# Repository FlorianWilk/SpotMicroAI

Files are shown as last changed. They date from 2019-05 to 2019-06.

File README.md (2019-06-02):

# SpotMicro AI 

I started this Project because i got inspired by some very smart People/Companies and Projects out there and want to 
understand and adapt their work. It is based on existing OpenSource-Projects and uses affordable Hardware to enable other people to build their own Bots and help us to understand how to control it the way we want.

This Project is heavily work in progress and may change every day. It is NOT a working or even finished Project you might want to use. 

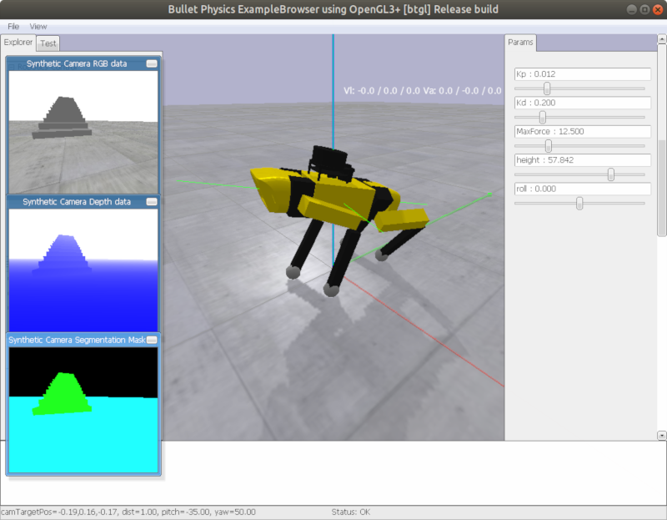
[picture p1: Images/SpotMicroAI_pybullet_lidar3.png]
PyBullet Simulation


[See the first movements of SpotMicroAI on YouTube](https://www.youtube.com/watch?v=vayiiII4xVQ)

Parts of this Project:
1. build a working physical Robot with cheap components everyone can build
2. create a simulated Environment and be able to control the Robot 
3. to do RL training to make it learn how to stand/walk/run

## 1. The physical Robot

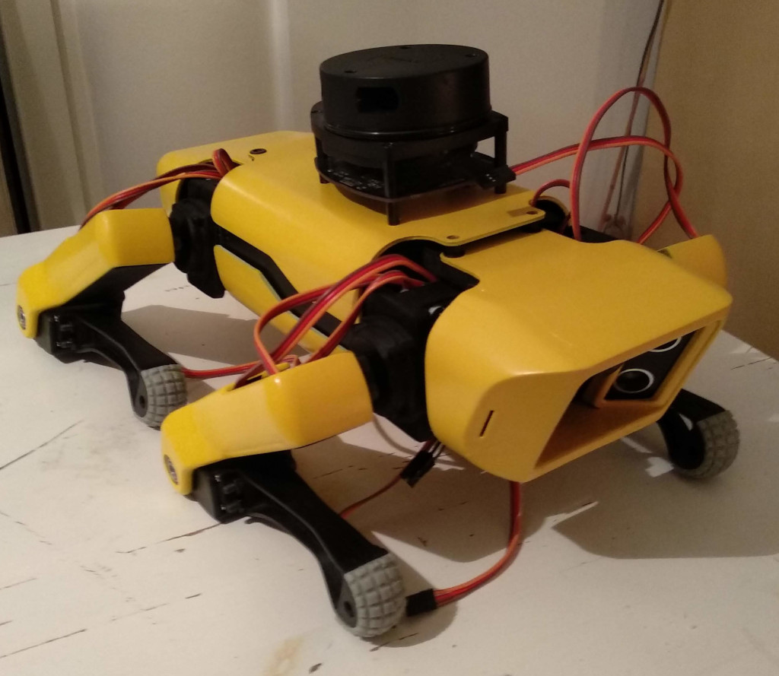
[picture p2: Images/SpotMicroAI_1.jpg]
SpotMicroAI


First of all thanks to Deok-yeon Kim aka KDY0523 who made [this incredible work on Thingiverse](https://www.thingiverse.com/thing:3445283)

This basically is the physical Robot. It will take some Days to print and assemble all the Parts, but it's worth all the effort. I also sanded, primed and painted all the Parts to give it a nicer Look.

[Here is my Thingiverse-Make](https://www.thingiverse.com/make:654812)

Since my setup required some additional Hardware, i recreated some parts using FreeCAD - see /Parts-Directory.

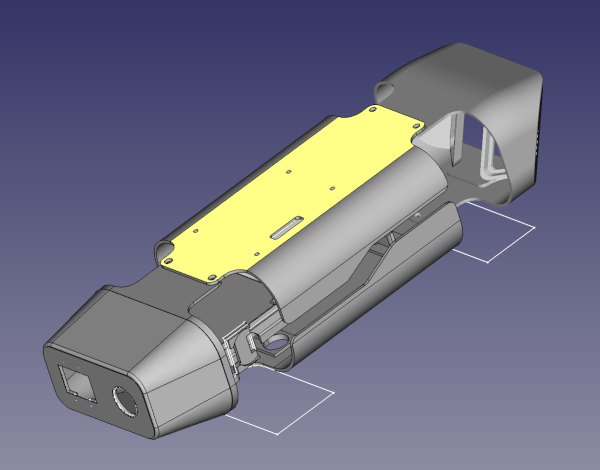
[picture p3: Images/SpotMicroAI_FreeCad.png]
Parts


### NVIDIA Jetson Nano

To have some Protection for the NVIDIA Jetson Nano i printed [this Case from Thingiverse](https://www.thingiverse.com/thing:3603594).

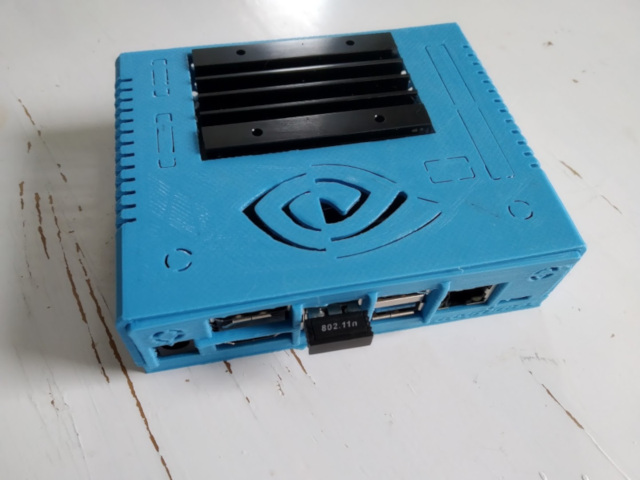
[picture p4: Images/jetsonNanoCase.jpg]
JetsonNano-Case


The Jetson Nano is connected to a 16 Channel PCA9685 I2C-Servo Driver which controls all the Servos. 
I will also try to connect the I2C OLED Display and the LED-Circle to it.

[Here you can find the all the Code for the Jetson Nano](/JetsonNano)

### Sensors

Since i am not a robotics company, i can't easily invest some hundreds of Euros/Dollars. So i will use Sonar Sensors instead of visual sensors like RGB or RGBD-Cams. Maybe i will try with ESPEyes or something in the near future.

Sensors used:
- 4 x HC-SR04-Sensors. 2x as in the original model in the front looking forward/down. 2x at the bottom (front/back) looking down to measure the ground-distance. 
- An IMU MPU-6050 is used to measure pitch,roll and velocities. Yaw will be ignored since it drifts quickly. 

Also i have a SSD1306 OLED-Display and a NeoMatrix LED-Circle i want to include for the Style.
In a first version i used an Arduino Mega as kind of Servo/Sensor-Controller and a Raspberry PI as Locomotion-Controller (communication via UART). But it showed up that the Arduino is too slow to handle Sensor-Signals and Servo-PWM properly at the same time. 

I am not sure if the Hardware i use now will be enough to finally have a very smooth walking Robot like for Example the real SpotMini. See this more as a Research-Project where I try to use cheap Hardware and other People's Work to learn more about how this all works. 

## 2. Simulation

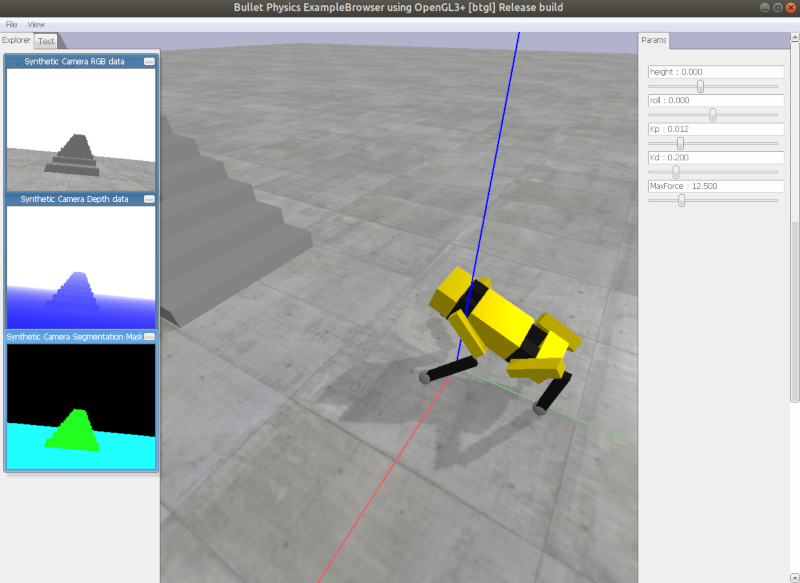
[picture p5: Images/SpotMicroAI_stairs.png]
PyBullet


I try to implement the Ideas of [this Paper](https://arxiv.org/pdf/1804.10332.pdf) by
Jie Tan, Tingnan Zhang, Erwin Coumans, Atil Iscen, Yunfei Bai, Danijar Hafner, Steven Bohez, and Vincent Vanhoucke
Google Brain,Google DeepMind

Here you can see the first version of the URDF-Model.

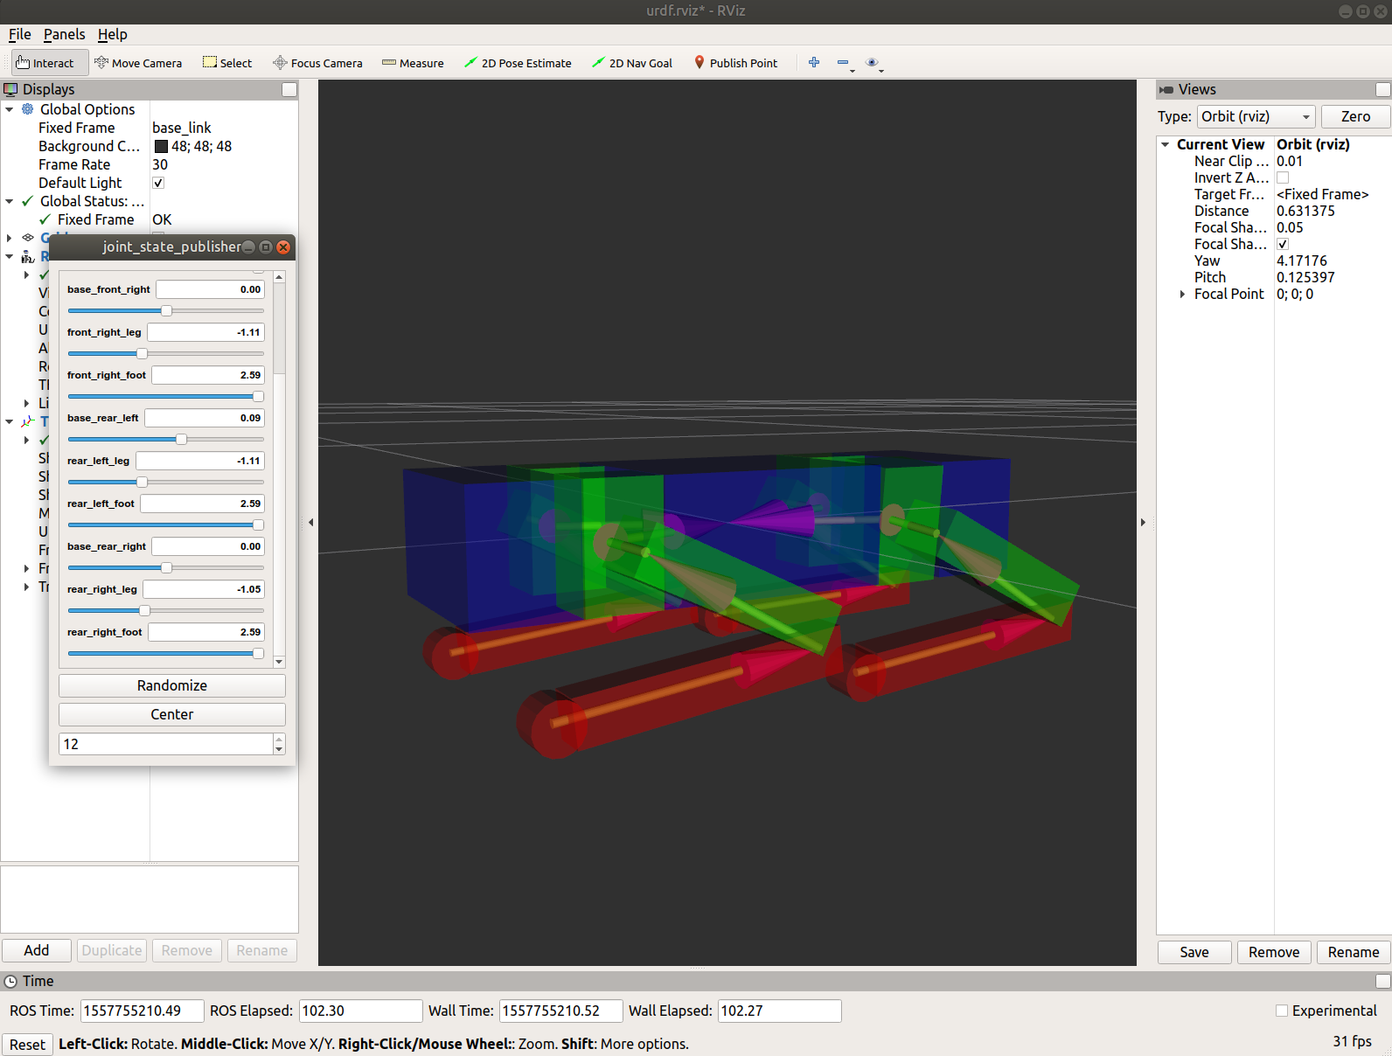
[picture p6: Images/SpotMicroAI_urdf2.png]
urdf


And here the Model with working Kinematics in a PyBullet-Simulation.

The URDF Model is very basic and work in progress. Masses and Inertias are guesses and not correct. I will have to disassemble the Robot to have correct weights. 

### Quickstart

This example can be found in the Repository. You need a GamePad for this to work:
```
pip3 install numpy
pip3 install pybullet
pip3 install inputs

cd Core/
python3 example_leg_motion.py
```

### Kinematics

In order to be able to move the Robot or event make it walk, we need something which tells us what servo-angles
will be needed for a Leg to reach position XYZ.
This is what InverseKinematics does. We know all the constraints, the length of the legs, how the joints rotate and where they are positioned. 

You can find [some a first draft of the calculations here](https://github.com/FlorianWilk/SpotMicroAI/tree/master/Kinematics). There is also a [Jupyter Notebook explaining the Kinematics](https://github.com/FlorianWilk/SpotMicroAI/tree/master/Kinematics/Kinematic.ipynb) and a [YouTube-Video](https://www.youtube.com/watch?v=VSkqhFok17Q).

## 3. Training

There is no real Training-Code yet.

## Credits and thanks

- Deok-yeon Kim creator of SpotMicro
- Boston Dynamics who built this incredible SpotMini,
- Ivan Krasin - https://ivankrasin.com/about/ - thanks for inspiration and chatting
- Jie Tan, Tingnan Zhang, Erwin Coumans, Atil Iscen, Yunfei Bai, Danijar Hafner, Steven Bohez, and Vincent Vanhoucke
Google Brain,Google DeepMind

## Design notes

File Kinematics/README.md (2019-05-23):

# How to solve Kinematics of a four-legged Robot

What is Kinematics / IK? 
A RobotLeg consists of 3 Servos rotating things from angle amin to angle amax.
When we know all three angles, we can determine the TargetPoint of the Leg.

This is what is called "Forward Kinematics". Inverse Kinematics is, you can imagine, the inverse. 
So, we have a Point and want to know the angles of our Servos. This can become pretty challenging when having more than 3-DOF (Degrees of Freedom).

See [this Page](https://www.ijstr.org/final-print/sep2017/Inverse-Kinematic-Analysis-Of-A-Quadruped-Robot.pdf) for more Information about Inverse Kinematics for quadruped Robots.
We will have to do our own calculations, since SpotMicro has some specialities which are not included a those formulas.

When you take a look at Fig. 2 you will notice, that the Leg used here is quite similar to 
SpotMicros Leg, but not really the same:

- the "Leg"-Motor/Rotation is on the same axis (z3) as the Shoulder-Motor/Rotation-Axis.
  SpotMicros Leg-Rotation is about 1cm lower, so we need an additional "L1b" which goes down (same direction as L2),
  but does not rotate with the Leg (L2,L3). Since we are completely recreating the calculations, i decided to go with
  L1-L4 instead of L1,L1b,L2,L3. 
- the "Foot"-joint is shifted by ~1cm to "the front" (pictures will follow). 

## Leg IK

So let's take a look at SpotMicro's Legs:

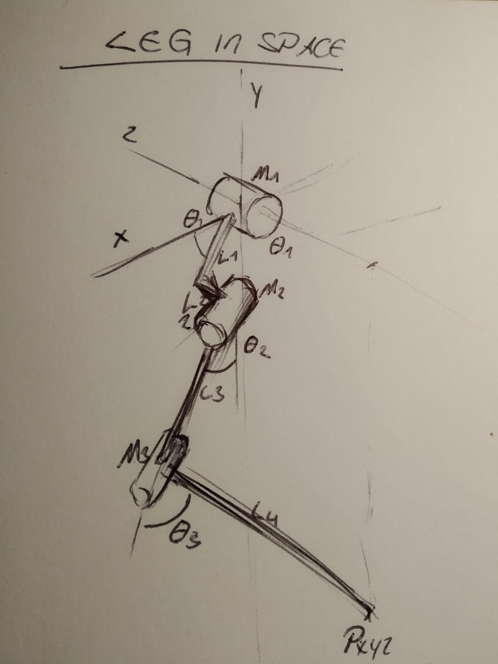
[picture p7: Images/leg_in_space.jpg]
Leg in Space


First of all lets focus on the shoulder-angle - theta1.
The Paper uses

Original

theta2

theta3

D

Let's discover that.
We need some kind of toolbelt for this mission.

### Tool 1: Pythagoras

Calculate the missing edge-length of a triangle with a 90° angle. 

Pythagoras

Pythagoras

Pythagoras

and so 

Pythagoras

Pythagoras

Pythagoras

### Tool 2: atan2(y,x) - get the angle of Point(x,y) from Origin (square-angle needed)

Please see [Wikipedia](https://en.wikipedia.org/wiki/Atan2). They did a great job in explaining it. 

### Tool 2b: get alpha angle of triangle when all sides are known

google

and yes, knowing that:

atan2

it looks very similar to:

D

theta3

### solving theta1 

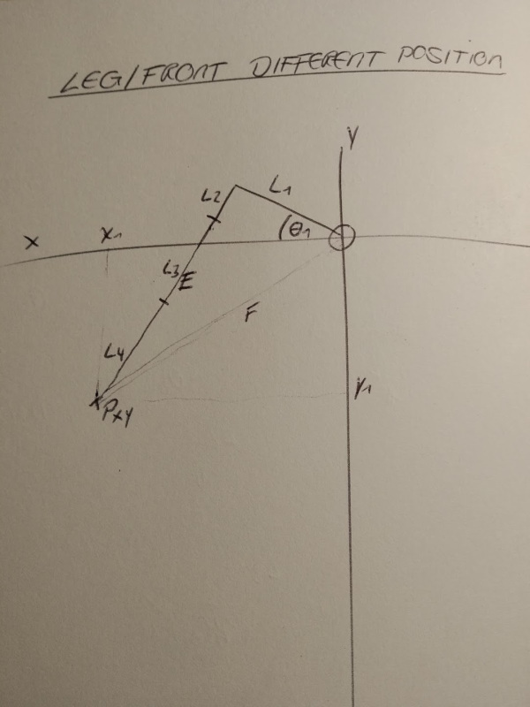
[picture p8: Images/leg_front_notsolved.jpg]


If we could solve E and F, we could calculate the angles and we have theta1!

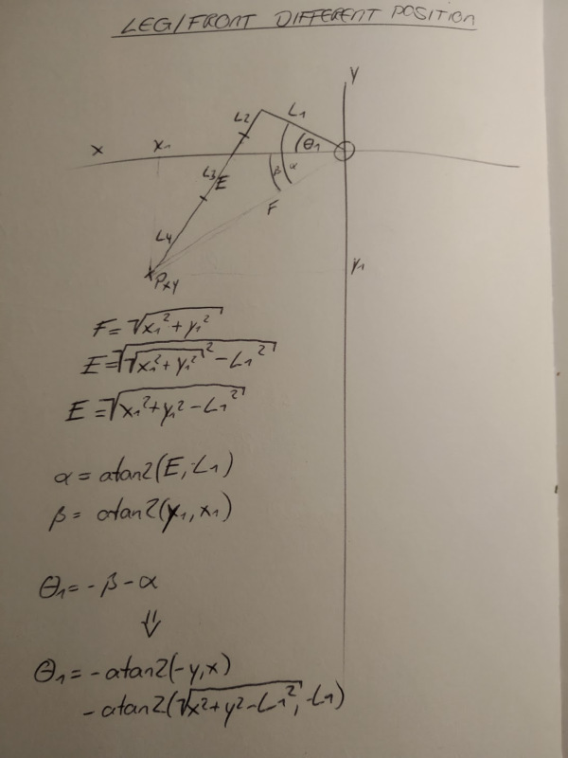
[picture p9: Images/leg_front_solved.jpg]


F is quite easy, as Pythagoras told us. And then E is quite easy too. Pythagoras again. 
Now we have a Triangle with L1,E and F, and it has a square-angle. Perfect for atan2!
So we calculate the whole angle alpha of the triangle and then substract the angle 
of the lower part by using atan2 again with -y and x. Great!

And now we have E. And E-L2 is "how long must the two joints leg and foot be (on X/Y only) to reach point Pxy".
We call it G.

g

So now we can say H is the "needed length of our joints in X,Y,Z". Thank you Pythagoras, again.

h

### solving theta3

We know what length we need to reach with the leg and foot-joint. It's a simple triangle.
All sides are known. L3,L4 and H.

D

theta3

### solving theta2

The last one, theta2. This one is quite easy:

Formula will follow

## Body Forward Kinematics

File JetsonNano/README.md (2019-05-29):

## SpotMicroAI for JetsonNano

The Nano will use a 16 Channel PCA9685 I2C-Servo Driver to drive the 12 Servos for the Legs.
First of all all prepare your Jetson Nano as you see in the NVIDIA Documentation.

Then connect to it via SSH and:

```
git clone https://github.com/FlorianWilk/SpotMicroAI.git
cd SpotMiroAI/JetsonNano
sudo apt-get install python3 python3-pip
pip3 install -U -r requirements.txt 
python3 start_robot.py
```

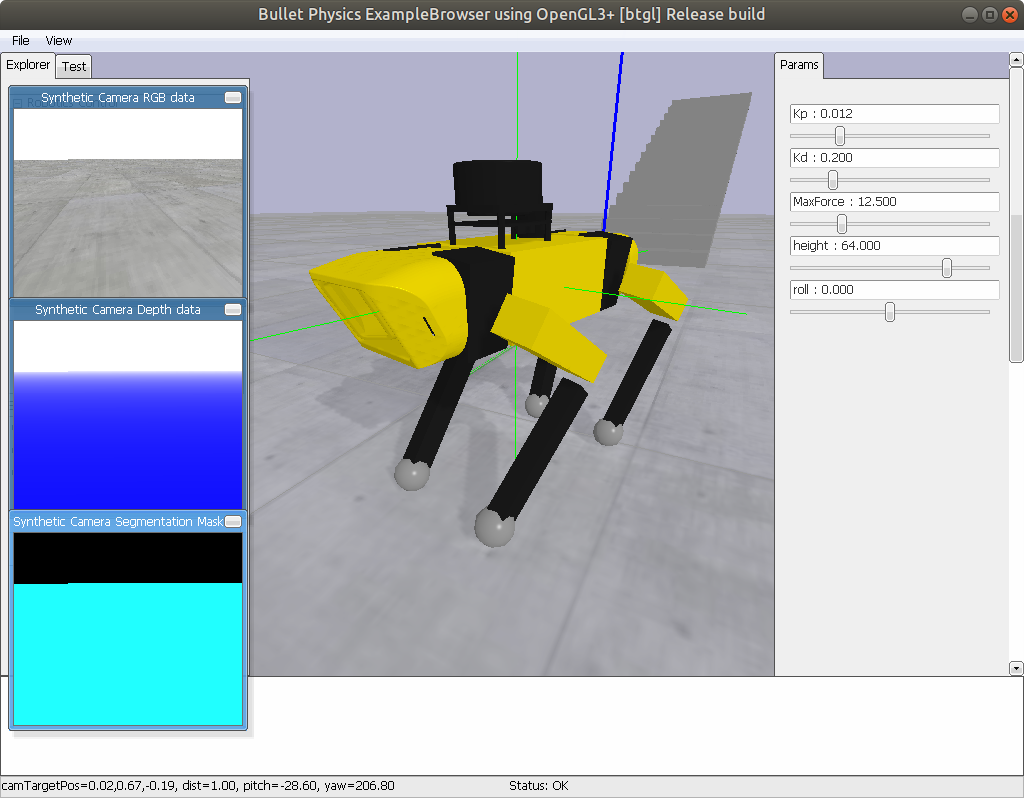
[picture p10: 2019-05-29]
Images/SpotMicroAI_pybullet_lidar.png

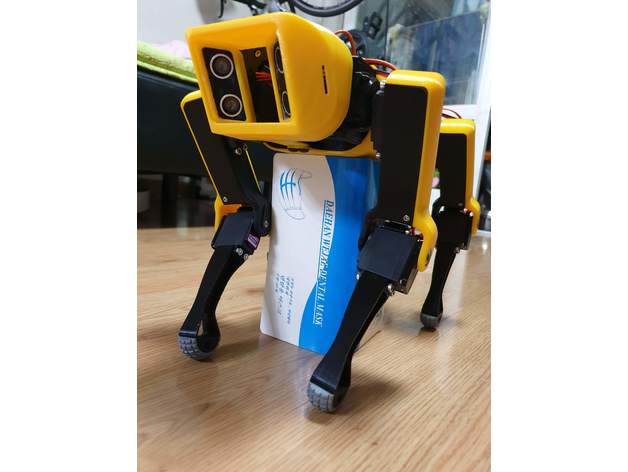
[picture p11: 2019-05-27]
STL/images/fc06bc6fa5a64951cc53c8cbf75a2861_preview_featured.jpg

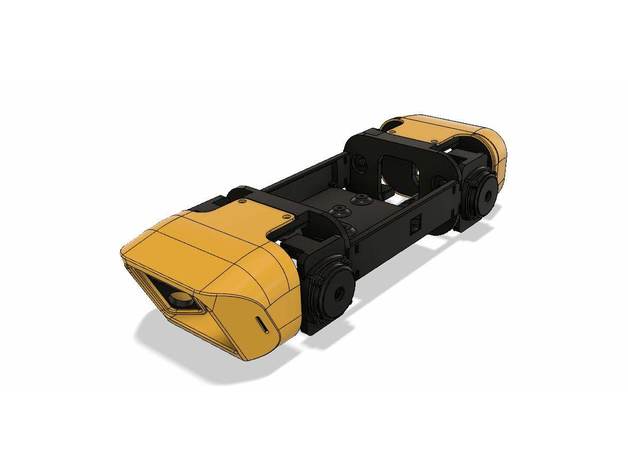
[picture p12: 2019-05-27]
STL/images/3bb4c0507fb43316081c01f398e9859c_preview_featured.jpg

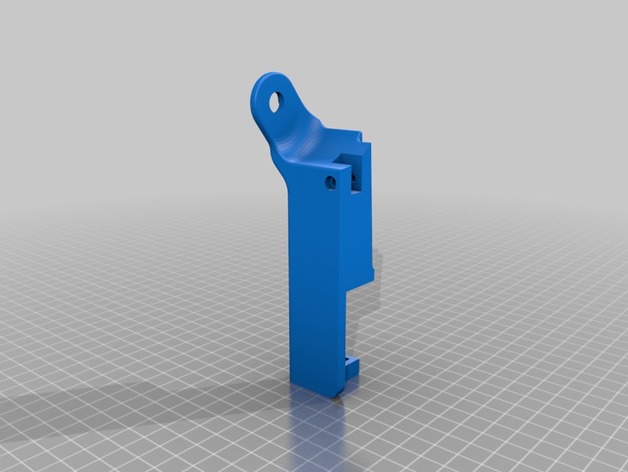
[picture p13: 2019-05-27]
STL/images/73ad5de99660dfc74a26c2a1477aee45_preview_featured.jpg

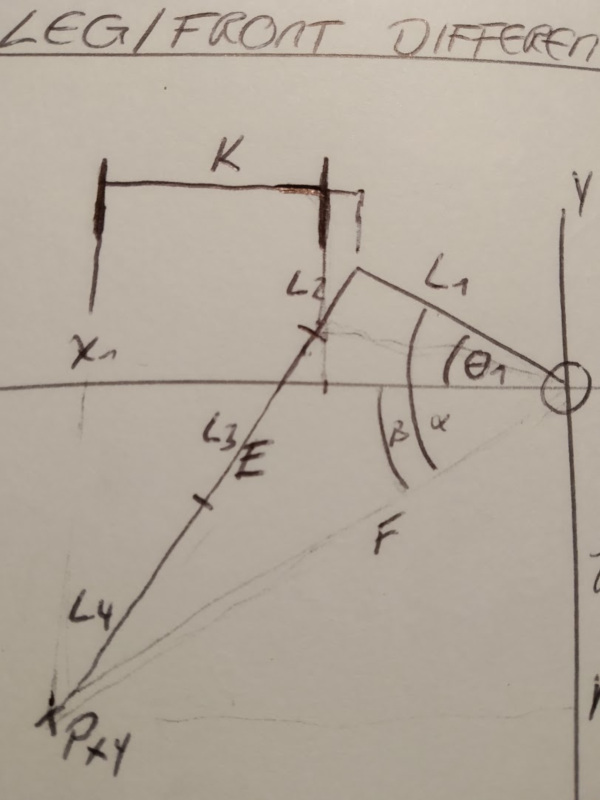
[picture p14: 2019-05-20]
Images/leg_front_k.jpg

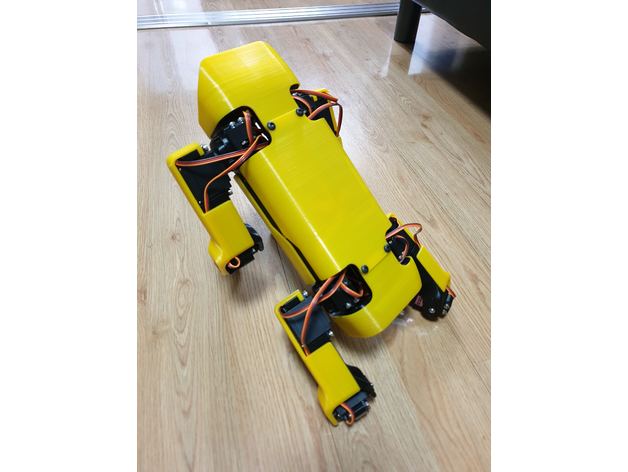
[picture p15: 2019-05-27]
STL/images/ada5e9392d64d278e71dfaec82ce3266_preview_featured.jpg

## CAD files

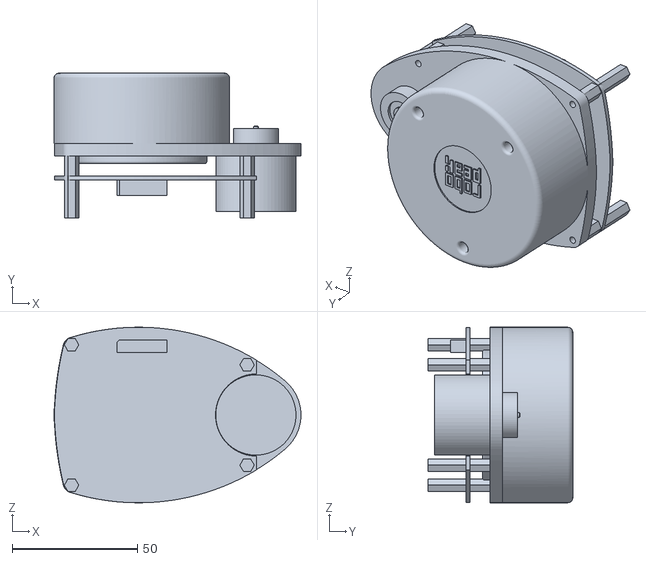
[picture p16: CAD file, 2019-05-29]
STL/lidar/rplidar_main.STL
98.5 x 57.7 x 70.0

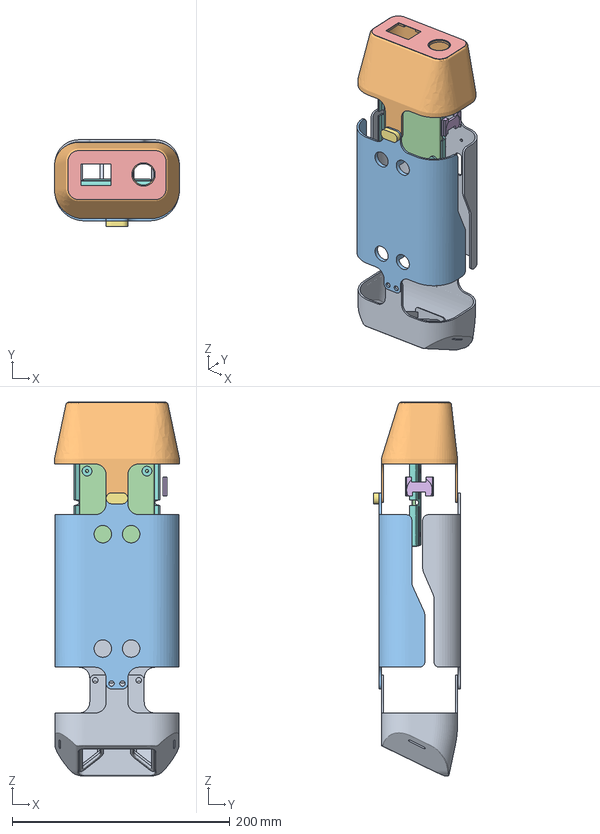
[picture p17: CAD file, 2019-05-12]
Parts/SpotMicroAI_AdditionalParts.FCStd
114.8 x 79.5 x 343.2 mm
Top
Rear
Bottom
BatteryHolderHolder
rearlabel
LEDMount
ScrewGuard
F_cover

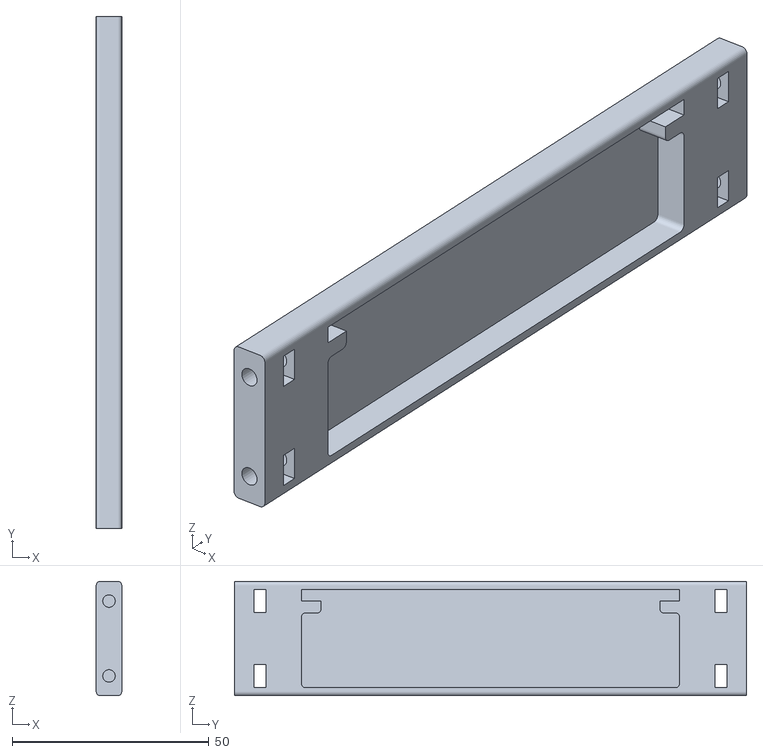
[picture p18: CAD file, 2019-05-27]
STL/files/R_side_plate.stl
6.50 x 130.0 x 29.0

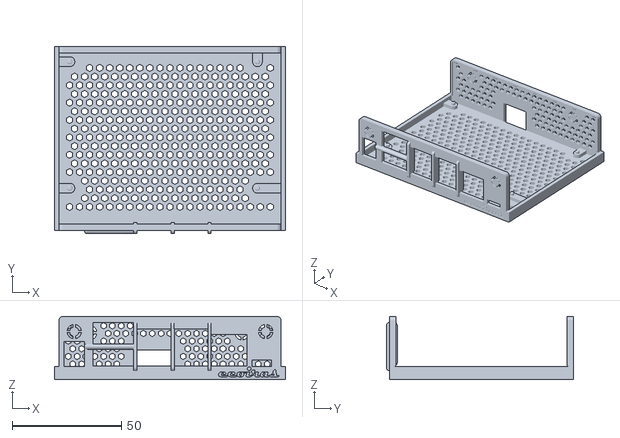
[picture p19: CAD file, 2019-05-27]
STL/jetsonnano/files/NanoBoxConnect_v11_Bottom.stl
105.9 x 85.8 x 29.0

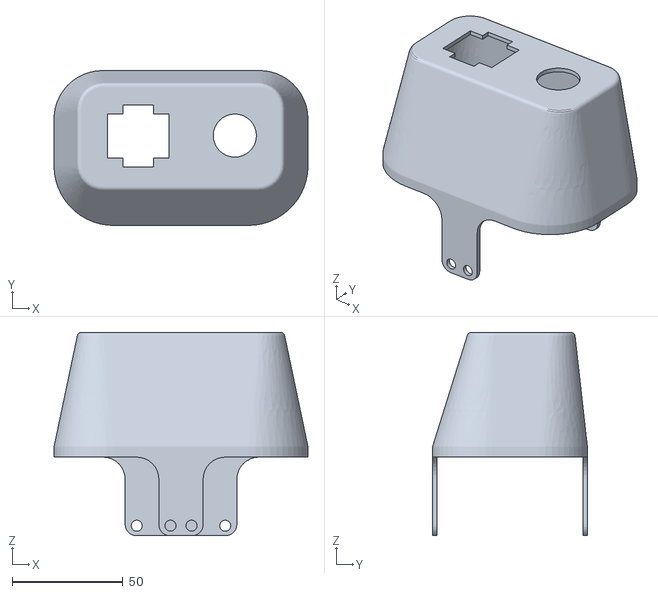
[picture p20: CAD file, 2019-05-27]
STL/rear2.stl
114.8 x 70.0 x 91.9

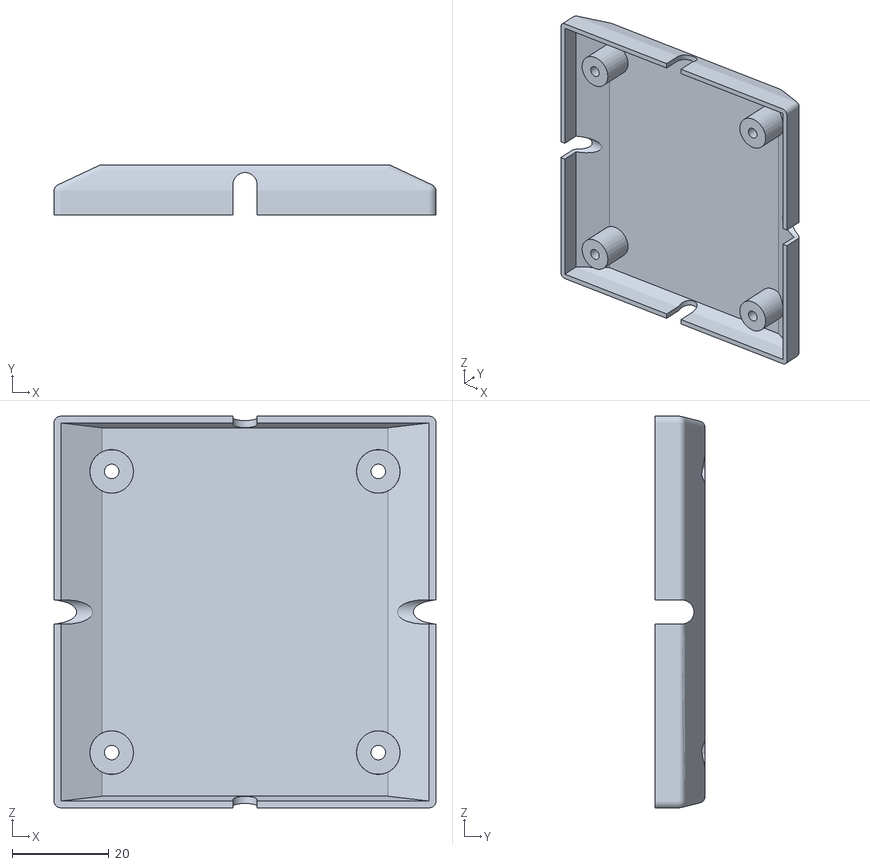
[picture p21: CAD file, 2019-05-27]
STL/batteryholder2.stl
78.8 x 10.4 x 80.8

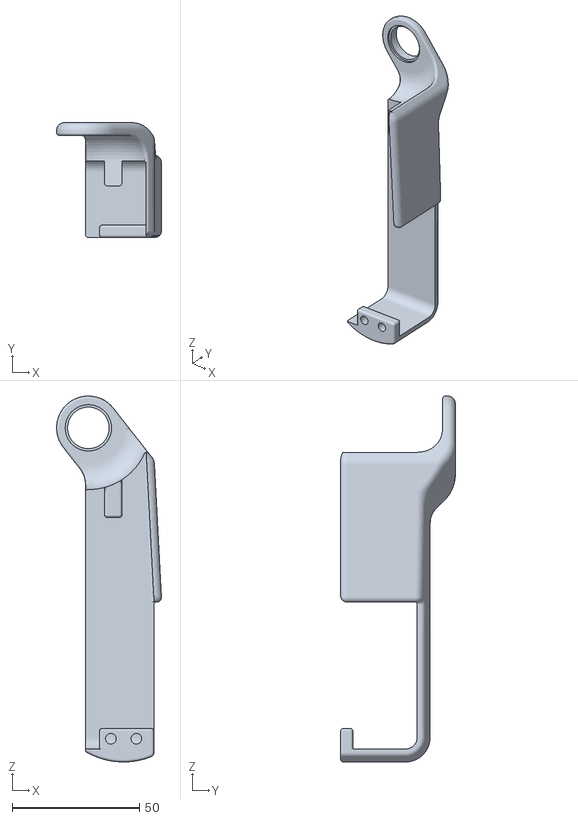
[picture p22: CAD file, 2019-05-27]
STL/files/L_arm_cover.stl
41.2 x 45.0 x 143.5

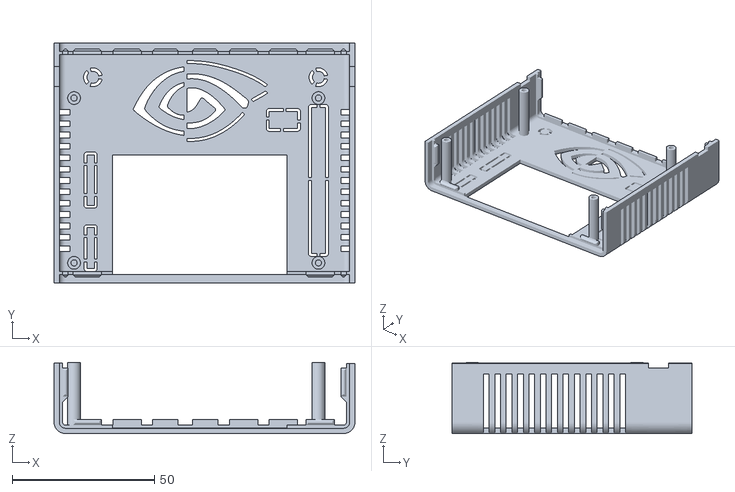
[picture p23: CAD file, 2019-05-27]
STL/jetsonnano/files/NanoBoxConnect_v11_Top.stl
105.9 x 84.3 x 25.0

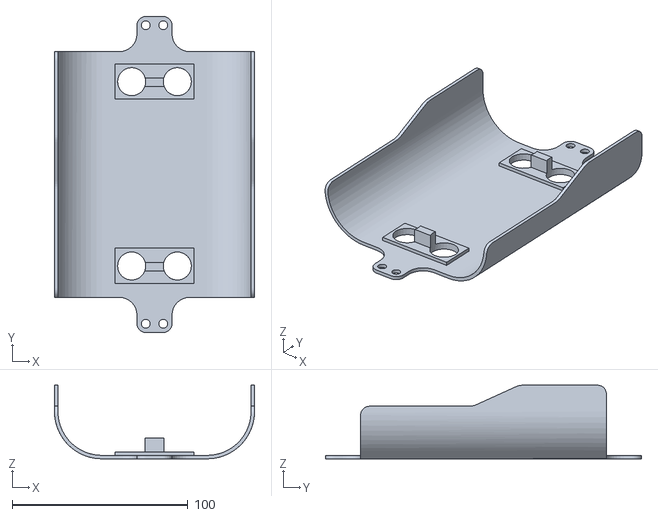
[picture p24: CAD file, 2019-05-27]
STL/bottom.stl
114.0 x 180.0 x 42.0

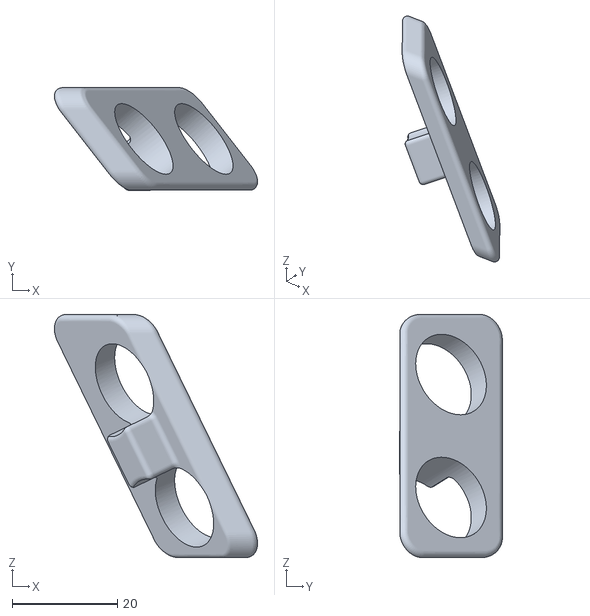
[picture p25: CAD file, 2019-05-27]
STL/files/L_ultra_sonic.stl
38.6 x 19.5 x 46.2

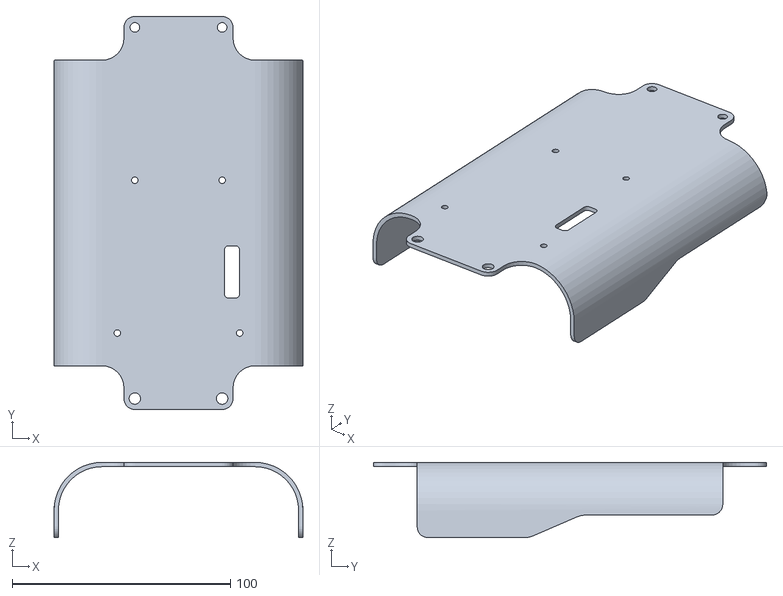
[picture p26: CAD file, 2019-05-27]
STL/top.stl
114.0 x 180.0 x 34.5

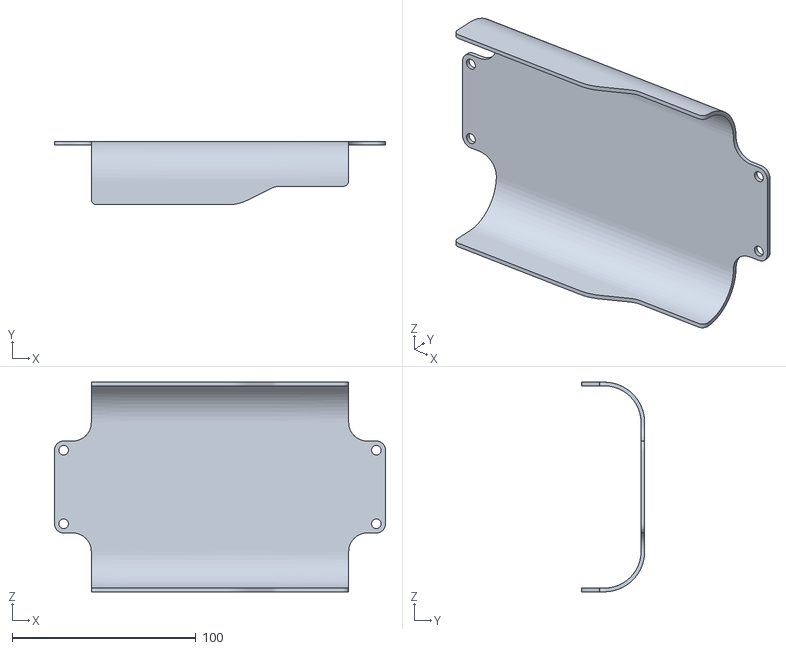
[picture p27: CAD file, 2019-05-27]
STL/files/non-mega_T_cover.stl
180.0 x 34.5 x 114.0

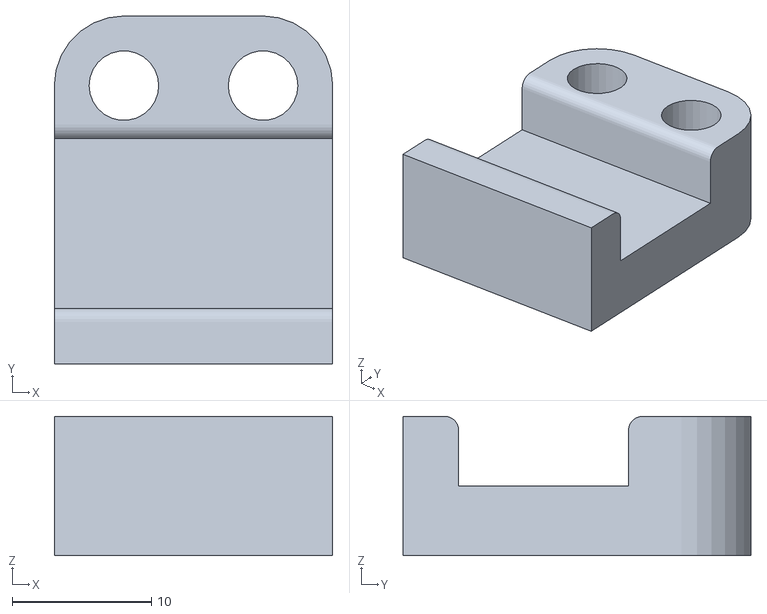
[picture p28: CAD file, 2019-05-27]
STL/testmount.stl
20.0 x 25.0 x 10.0

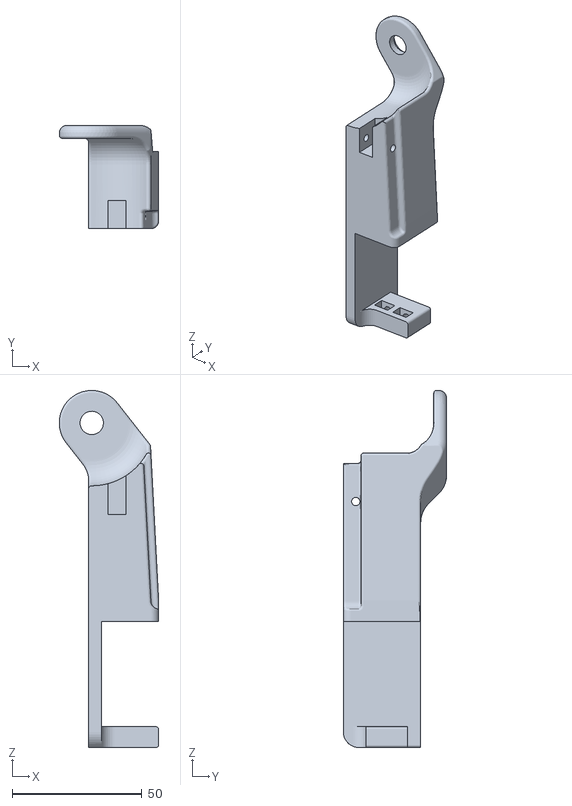
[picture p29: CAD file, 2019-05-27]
STL/files/R_arm.stl
38.2 x 39.8 x 137.4

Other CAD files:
STL/files/non-mega_L_side_plate.stl
STL/ledholder.stl
STL/files/R_arm_joint.stl
STL/batteryholder.stl
STL/files/B_cover.stl
STL/files/F_cover.stl
STL/files/F_cover_orig.stl
STL/files/F_shoulder.stl
STL/files/L_arm.stl
STL/files/L_arm_joint.stl
STL/files/L_side_plate.stl
STL/files/L_wrist.stl
STL/files/R_arm_cover.stl
STL/files/R_cover.stl
STL/files/R_shoulder.stl
STL/files/R_ultra_sonic.stl
STL/files/R_wrist.stl
STL/files/T_cover.stl
STL/files/foot.stl
STL/files/non-mega_B_cover.stl
STL/files/plate.stl
STL/label.stl
STL/rear.stl
STL/screwguard.stl

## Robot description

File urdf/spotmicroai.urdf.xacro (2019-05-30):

<?xml version="1.0"?>
<robot xmlns:xacro="http://www.ros.org/wiki/xacro" name="SpotMicroAI">

  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

  <xacro:property name="body_length" value="0.140" />
  <xacro:property name="body_width" value="0.110" />
  <xacro:property name="body_height" value="0.070" />

  <xacro:property name="lidar_length" value="0.0985" />
  <xacro:property name="lidar_width" value="0.0577" />
  <xacro:property name="lidar_height" value="0.070" />


  <xacro:property name="front_length" value="0.058" />
  <xacro:property name="rear_length" value="0.040" />

  <xacro:property name="shoulder_length" value="0.044" />
  <xacro:property name="shoulder_width" value="0.038" />

  <xacro:property name="leg_length" value="0.120" />
  <xacro:property name="foot_length" value="0.155" />

  <xacro:property name="toe_radius" value="0.020" />
  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
  <xacro:property name="toe_width" value="0.020" />
  <xacro:property name="shift" value="0.052" />
  <xacro:property name="shiftx" value="0.093" />
  <xacro:property name="shifty" value="0.036" />

  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

  <xacro:macro name="gen_shoulder" params="name left">
    <link name="${name}">
      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
      <inertial>
        <mass value="0.10"/>
        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
      </inertial>
    </link>
  </xacro:macro>

  <xacro:macro name="gen_shoulder_joint" params="pos shiftx shifty">
    <joint name="${pos}_shoulder" type="revolute">
      <parent link="base_link"/>
      <child link="${pos}_shoulder_link"/>
      <axis xyz="1 0 0"/>
      <origin rpy="0 0 0" xyz="${shiftx} ${shifty} 0"/>
      <limit effort="1000.0" lower="-0.548" upper="0.548" velocity="0.7"/>
      <dynamics damping="0.0" friction="0.5"/>
    </joint>
  </xacro:macro>

  <xacro:macro name="gen_leg" params="name">
    <link name="${name}">
      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
      <inertial>
        <mass value="0.15"/>
        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
      </inertial>
    </link>
  </xacro:macro>

  <xacro:macro name="gen_leg_joint" params="pos shift">
    <joint name="${pos}_leg" type="revolute">
      <parent link="${pos}_shoulder_link"/>
      <child link="${pos}_leg_link"/>
      <axis xyz="0 1 0"/>
      <origin rpy="0 0 0" xyz="0 ${shift} 0"/>
      <limit effort="1000.0" lower="-2.666" upper="1.548" velocity="0.5"/>
      <dynamics damping="0.0" friction="0.0"/>
    </joint>
  </xacro:macro>

  <xacro:macro name="gen_foot" params="name">
    <link name="${name}">
      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
      <inertial>
        <mass value="0.1"/>
        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
      </inertial>
    </link>
  </xacro:macro>

  <xacro:macro name="gen_foot_joint" params="pos">
    <joint name="${pos}_foot" type="revolute">
      <parent link="${pos}_leg_link"/>
      <child link="${pos}_foot_link"/>
      <axis xyz="0 1 0"/>
      <origin rpy="0 0 0" xyz="-0.01 0 -${leg_length}"/>
      <limit effort="1000.0" lower="-0.1" upper="2.59" velocity="0.5"/>
      <dynamics damping="0.0" friction="0.5"/>
    </joint>
  </xacro:macro>

  <xacro:macro name="gen_toe" params="name">
    <link name="${name}">
      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
      <inertial>
        <mass value="0.05"/>
        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
      </inertial>
    </link>
  </xacro:macro>

 <xacro:macro name="gen_toe_joint" params="pos">
    <joint name="${pos}_toe" type="fixed">
      <parent link="${pos}_foot_link"/>
      <child link="${pos}_toe_link"/>
      <origin xyz="0 0 -${foot_length+0.01}"/>
    </joint>
  </xacro:macro>

  <xacro:macro name="gen_full_leg_joint" params="pos shiftx shifty shift left">
    <xacro:gen_shoulder name="${pos}_shoulder_link" left="${left}"/>
    <xacro:gen_leg name="${pos}_leg_link"/>
    <xacro:gen_foot name="${pos}_foot_link"/>
    <xacro:gen_toe name="${pos}_toe_link"/>

    <xacro:gen_shoulder_joint pos="${pos}" shiftx="${shiftx}" shifty="${shifty}"/>
    <xacro:gen_leg_joint pos="${pos}" shift="${shift}"/>
    <xacro:gen_foot_joint pos="${pos}"/>
    <xacro:gen_toe_joint pos="${pos}"/>
  </xacro:macro>

  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

  <link name="base_link">
    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
    <inertial>
      <mass value="0.80"/>
      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
    </inertial>
  </link>

  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

   <link name="lidar_link">
    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
    <inertial>
      <mass value="0.50"/>
      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
    </inertial>
  </link>
  <joint name="base_lidar" type="fixed">
    <parent link="base_link"/>
    <child link="lidar_link"/>
        <origin xyz="0 0 ${body_height/2}"/>
  </joint>  

  <link name="rear_link">
    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
    <inertial>
      <mass value="0.20"/>
      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
    </inertial>
  </link>
  <joint name="base_rear" type="fixed">
    <parent link="base_link"/>
    <child link="rear_link"/>
  </joint>

  <link name="front_link">
    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
    <inertial>
      <mass value="0.20"/>
      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
    </inertial>

  </link>
  <joint name="base_front" type="fixed">
    <parent link="base_link"/>
    <child link="front_link"/>
  </joint>

  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

  <xacro:gen_full_leg_joint pos="front_left" shiftx="-${shiftx}" shifty="-${shifty}" shift="-${shift}" left="true"/>
  <xacro:gen_full_leg_joint pos="front_right" shiftx="-${shiftx}" shifty="${shifty}" shift="${shift}" left="false"/>
  <xacro:gen_full_leg_joint pos="rear_left" shiftx="${shiftx}" shifty="-${shifty}" shift="-${shift}" left="true"/>
  <xacro:gen_full_leg_joint pos="rear_right" shiftx="${shiftx}" shifty="${shifty}" shift="${shift}" left="false"/>

</robot>

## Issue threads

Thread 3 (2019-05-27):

Python 2.7 compatibility

FlorianWilk, 2019-05-27:
Interesting... when running
python3 gamepad.py
everything works. The Bot falls to the ground and keeps standing.
When i use python 2.7:
python gamepad.py
The Bot falls down. The left and right legs have different positions. Why is that?!

littleggghost, 2019-05-27:
I use python2.7 now, here is the initial pose:
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

FlorianWilk, 2019-05-27:
Yes, same here. I will keep on using Python3 to have some progress on the
Kinematics.
Maybe you want to investigate this bug? I have no clue why Python2.7 should
do different calculations than Python3 does.

On Mon, May 27, 2019 at 1:50 PM littleggghost <notifications@github.com>
wrote:

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

littleggghost, 2019-05-27:
Maybe the initial command caused this.
You can try this initial pose in gamepad.py:
`line224    angles = kin.calcIK(Lp, (math.pi/180*roll, 0, 0), (100/256*-joy_rz-20+100, 40+height, joy_x))`

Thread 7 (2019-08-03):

Where can I find the STL file for a plate to mount an Nvidia Jetson Nano?

ashishk88, 2019-08-03:
Great work on the Spot Micro and thanks for open sourcing your work! I will really appreciate if you could point me to the location of a plate to mount an Nvidia Jetson Nano.

ashishk88, 2019-08-03:
It will be great if you could also upload the STL for the top cover with holes for LiDAR mounting.

jdmueller, 2019-08-03:
https://github.com/FlorianWilk/SpotMicroAI/blob/master/STL/top.stl

jdmueller, 2019-08-03:
https://github.com/FlorianWilk/SpotMicroAI/blob/master/urdf/stl/jetsonPlate.stl

ashishk88, 2019-08-03:
Thanks a lot!

Closed 2019-08-03.

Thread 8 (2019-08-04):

Electrical Wiring Diagram

mschwab87, 2019-08-04:
Could you possibly provide a wiring diagram?

jimprince, 2019-08-16:
what hardware are you looking for a wiring diagram for? For the PCA 9685 to the Jetson Nano or for the servos to the PCA9685? Or something else?

mschwab87, 2019-08-16:
Hey Brad,

We were able to figure it out. When we started the project we were just
wondering if there was a wiring diagram for the the whole system servos to
pca, pca to jetson etc. Thanks for getting back to me.

Regards,

Matt

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

jimprince, 2019-08-16:
No worries. Let me know if you have any other questions.

Closed 2019-08-17.

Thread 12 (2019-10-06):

Problems with running the examples - stl files

Brudasoe, 2019-10-06:
Hey, so I had some problems with running the bullet python examples, the source of those problems is that thought the stl files have beenample moved, urdf files haven't really been updated (rplidar_main.stl is missing and some tags point to foot.stl in STL folder (which has been removed). I can make a PR to fix this issues if you want :slightly_smiling_face:

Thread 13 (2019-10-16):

kinematic.py file is lost

mushroom-x, 2019-10-16:
after excute  the first cell of script   `Kinematic/KinematicMovements.ipynb , `
error message as bellow:
```
---------------------------------------------------------------------------
ModuleNotFoundError                       Traceback (most recent call last)
<ipython-input-2-905fcd046da8> in <module>
      6 import pybullet as p
      7 import pybullet_data
----> 8 from kinematics import Kinematic
      9
     10 p.connect(p.DIRECT)

ModuleNotFoundError: No module named 'kinematics'

```

Brudasoe, 2019-10-21:
Parts of code have been moved, but I guess not all parts have been updated ( I had an issue with stl files),  seems like you need to modify the code to point to Core/kinematics.py or copy the kinematics.py to the same directory

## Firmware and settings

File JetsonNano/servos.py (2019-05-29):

"""
Class to Control the Servos for all Legs
"""
import Adafruit_PCA9685
import board
import busio
from adafruit_servokit import ServoKit

class Servo:
    def __init__(self,direction,servo):
        self.direction=direction
        self.offset=0
        self.min=0
        self.max=180
        self.servo=servo
        self.lastValue=0

    def setValue(self,value):
        self.lastValue=value
        realValue=self.offset+self.direction*value
        # I2C set calculated Value - current dummy is servo center
        self.servo.angle=realValue
    
    def getLastValue(self):
        return self.lastValue

    def setOffset(self,offset):
        self.offset=offset
        self.setValue(self.getLastValue())

class AcceleratedServo(Servo):
    def __init__(self,direction,servo):
        Servo.__init__(self,direction,servo)

        # random values for now
        self.kp=0.2
        self.kd=0.2
        self.max_acceleration=14

    def moveTo(self,value,inTime):
        print("Moving servo to {} in {}ms".format(value,inTime))

class Servos:

    def __init__(self):
        print("Servos init")

        i2c = busio.I2C(board.SCL, board.SDA)
        self.pca = Adafruit_PCA9685.PCA9685(i2c)
        #self.pca = Adafruit_PCA9685.PCA9685(address=0x40)
        kit = ServoKit(channels=16)

        # Front_left,Front_right,Back_left,Back_right
        # each leg has shoulder, leg, foot
        directions=[-1,1,1,1,1,1,-1,1,1,1,1,1]
        self.leg_servos=[AcceleratedServo(directions[x],kit.servo[x]) for x in range(0,12)]

    def setServoPositions(self,positions):
        [self.leg_servos[x].moveTo(positions[x],100) for x in range(0,12)]
    
    def getServoOffset(self,servo):
        return self.leg_servos[servo].offset

    def setServoOffset(self,servo,offset):
        self.leg_servos[servo].setOffset(offset)

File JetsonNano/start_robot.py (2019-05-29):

import time
import math
import numpy as np
from kinematics import Kinematic
from servos import Servos
class RobotRunner:

    def __init__(self):
        print("Initialising")
        self.servos=Servos()
        self.Kinematic=Kinematic()

        self.servos.setServoPositions([0 for _ in range(0,12)])

    def calibrate(self):
        print("Running")
        servo=int(input("Enter Servo to calibrate (0-12)"))
        print("Current Offset is {}".format(self.servos.getServoOffset(servo)))
        offset=int(input("Enter new Offset:"))
        self.servos.setServoOffset(servo,offset)


RobotRunner().calibrate()

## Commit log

2019-05-13 Added round toes to URDF
2019-05-13 Hello PyBullet
    [plane.obj, plane.urdf]
2019-05-13 URDF colors
2019-05-13 xacro for urdf
    [spotmicroai.urdf.xacro]
2019-05-13 xacro URDF improvements
    [spotmicroai.urdf.xacro]
2019-05-13 further xacro improvements. < 200lines now
    [spotmicroai.urdf.xacro]
2019-05-13 added mass and dynamics
    [spotmicroai.urdf.xacro]
2019-05-13 URDF improvements
    [spotmicroai.urdf.xacro]
2019-05-13 Playing with dynamics
    [spotmicroai.urdf.xacro]
2019-05-14 First Leg moves and some typos fixed
2019-05-17 Jetson Nano
2019-05-19 Inverse Kinematics first Impl
2019-05-21 Inverse Kinematics
2019-05-22 Jupyter Body Forward Kinematics
2019-05-23 Kinematics / Leg + Body
2019-05-23 Kinematics README update
2019-05-23 Kinematic finished
2019-05-23 Kinematics Simulation
2019-05-23 Camera adjustments
2019-05-24 Code cleanups
    [spotmicroai.urdf.xacro]
2019-05-24 added Stairs
    [stairs.urdf.xacro]
2019-05-29 Lidar added to URDF
    [rplidar_main.STL, spotmicroai.urdf.xacro]
2019-05-29 Jetson Nano Code
    [plane.obj, plane.urdf, spotmicroai.urdf.xacro]
2019-05-29 Added first Version of ServoCalibration
2019-05-29 I2C Servo init
2019-05-30 trotting gait
    [spotmicroai.urdf.xacro]
